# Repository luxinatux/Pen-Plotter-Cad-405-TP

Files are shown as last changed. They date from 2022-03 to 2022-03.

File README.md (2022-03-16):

# Pen-Plotter-Cad-405-TP
 This Repository was created to show the ME 405 pen-plotter CAD repository. It contains the STL files for print as well. This repository contains manufacturing pictures as well as documents necessary to build the project.

## **Description of Project**
Our Hardware Design is broken up into three parts: the drop down table base, the track, and the sled. The drop down table base allows us to have a half degree of freedom by being in up(pen down) or in the down position (pen up). We used a 12V continuous pull solenoid, actuated with an N-channel Mosfet with a 5V Gate to Source start voltage. This in conjuction with a flyback diode, and two 4 inch springs, allowed for our drawing surface to be dropped and not be in contact with the pen. The sled was the mover of the pen. Two 3D printed side rails created a track for our pen holder. The pen holder moved along this track being guided by 6mm GT2 timing belt that was directly mounted to the holder. The belt was driven by a 48 tooth plastic gear that was geared to the provided ME 405 bin Pittperson Gearmotors. The side rails were epoxied to a 4"x13"x0.375" piece of particle board with a slot cut through the middle of it. The conjunction of the drop down table base and the sled were through the "elbow motor". The "elbow motor" was a 131:1 12V DC motor that was clamped down to a 3D printed motor mount. This motor mount was epoxied to the top of the drop down table ledge, and the nucleo is mounted next to it. The elbow motor shaft ran through the particle board sled, and interfaced with a shaft collar epoxied to the surface. In order to allow free motion of the sled across the drawing plane, a caster wheel was epoxied to the end of the sled, opposite of the elbow motor and shaft collar. A sawed off skateboard truck provided an appropriate solution. The track for the skateboard wheel was created such that the sled would be level when moving left and right. To protect the system, two limit switches were added: one on the pen holder slider, and one on the skateboard wheel track. These two limit switches were used as zeroing points in our code.

The Bill of Materials is at the bottom of the README

## **Functional Prototype**
Included Below is a link to our plotter drawing a smiley face: 
https://youtu.be/C0HX3mLi9cc

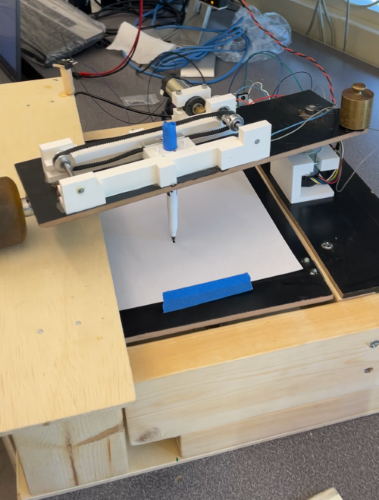
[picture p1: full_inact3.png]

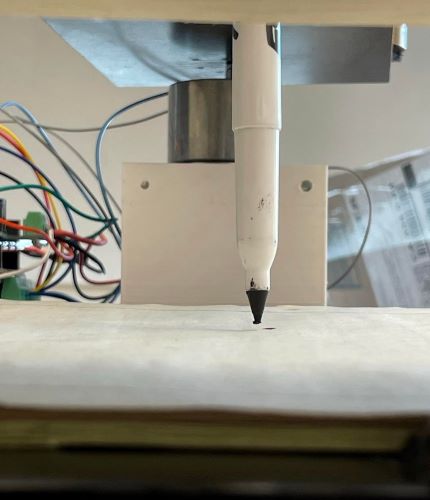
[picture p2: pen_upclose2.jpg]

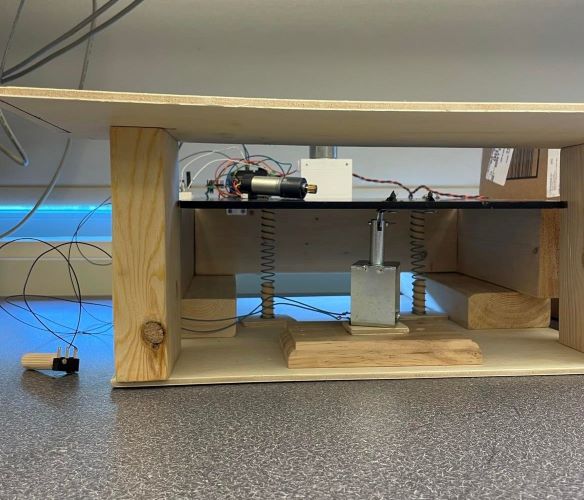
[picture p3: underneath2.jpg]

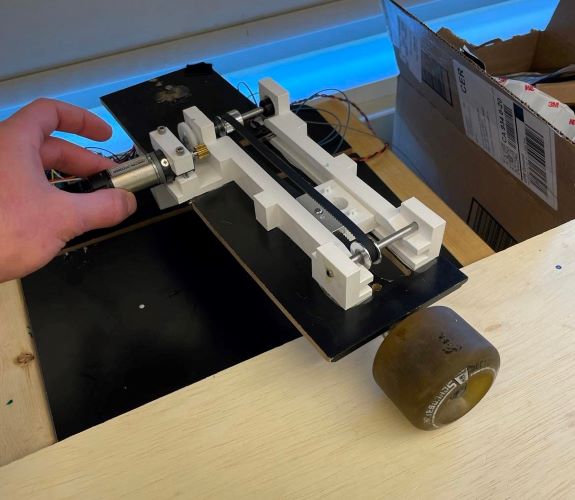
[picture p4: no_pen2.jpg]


## **CAD Model**
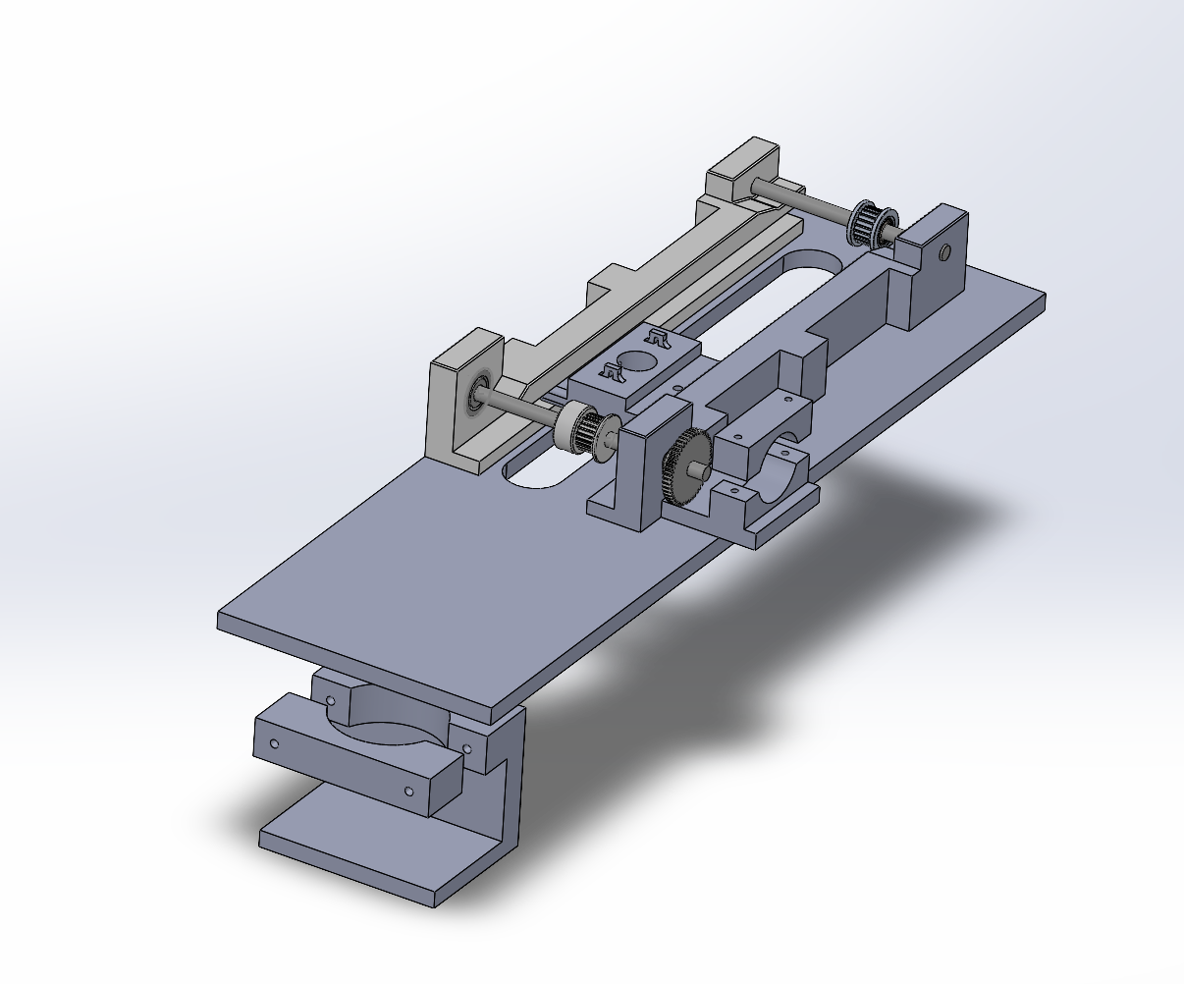
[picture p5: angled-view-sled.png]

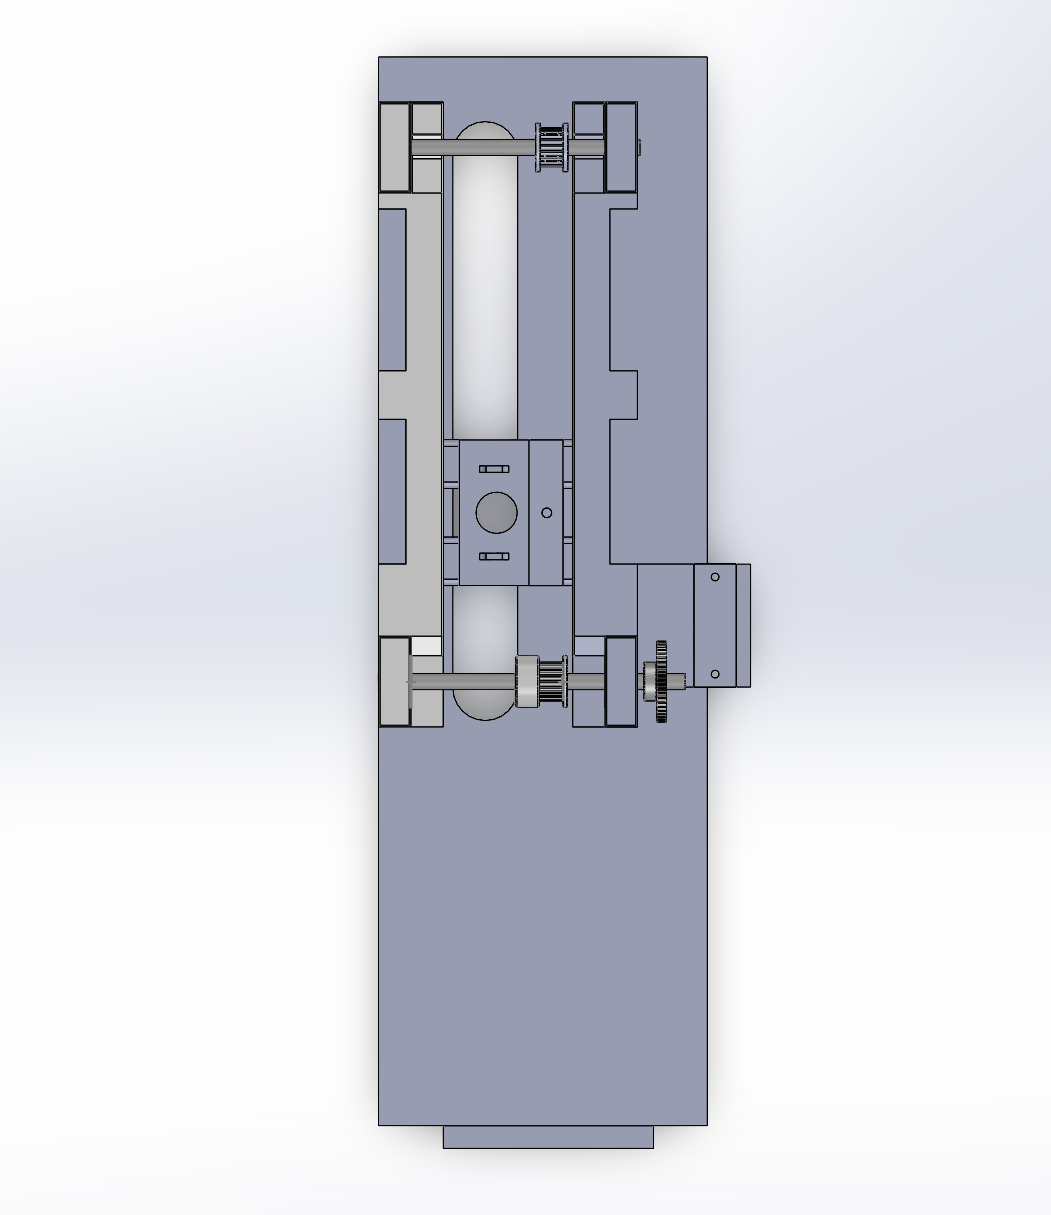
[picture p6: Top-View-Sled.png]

## **Drawings**
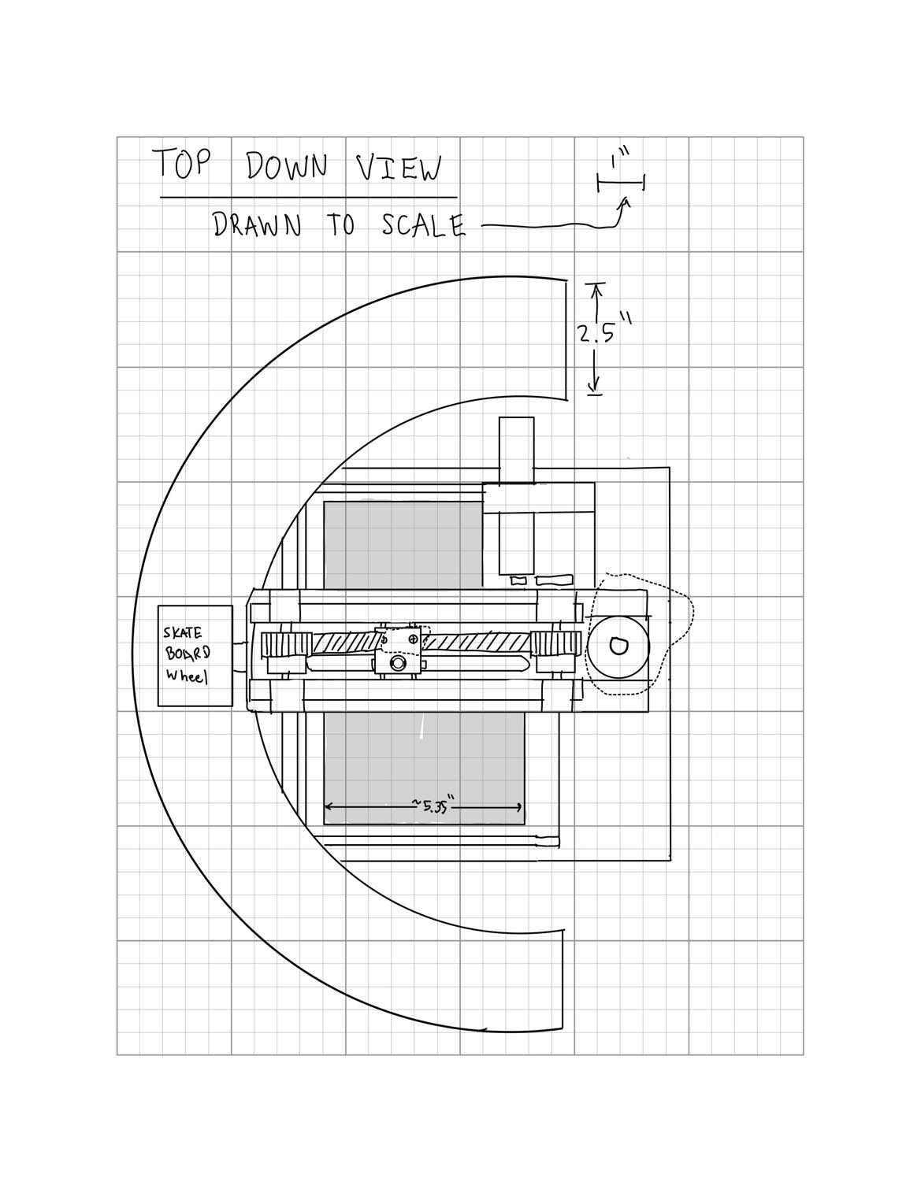
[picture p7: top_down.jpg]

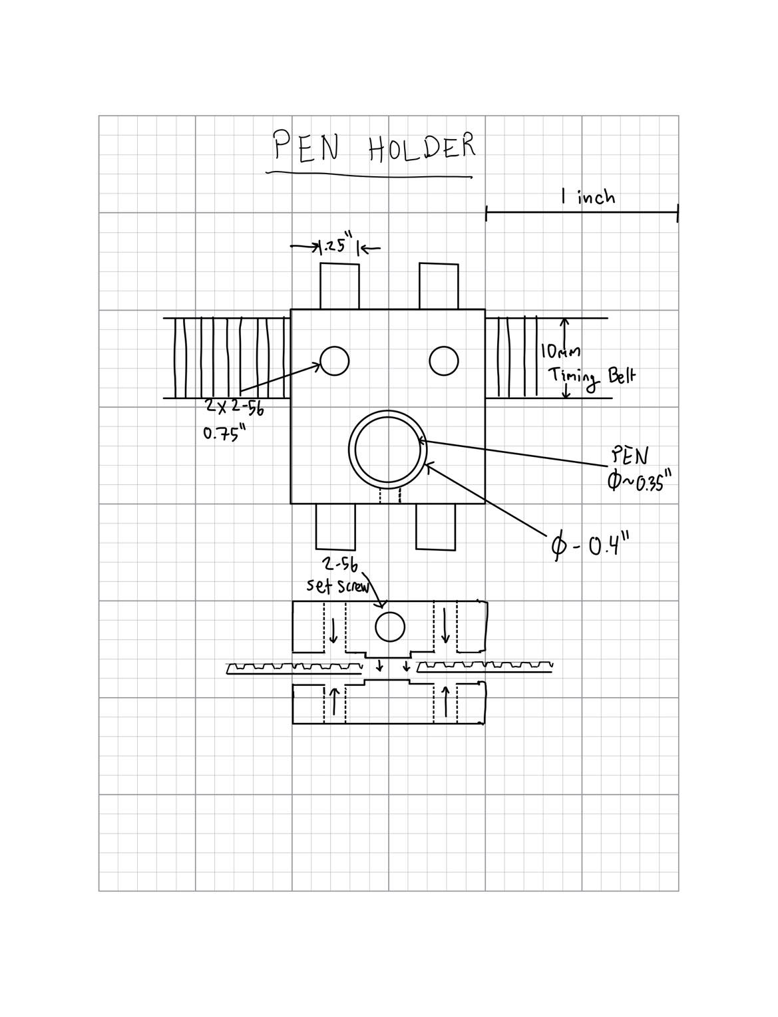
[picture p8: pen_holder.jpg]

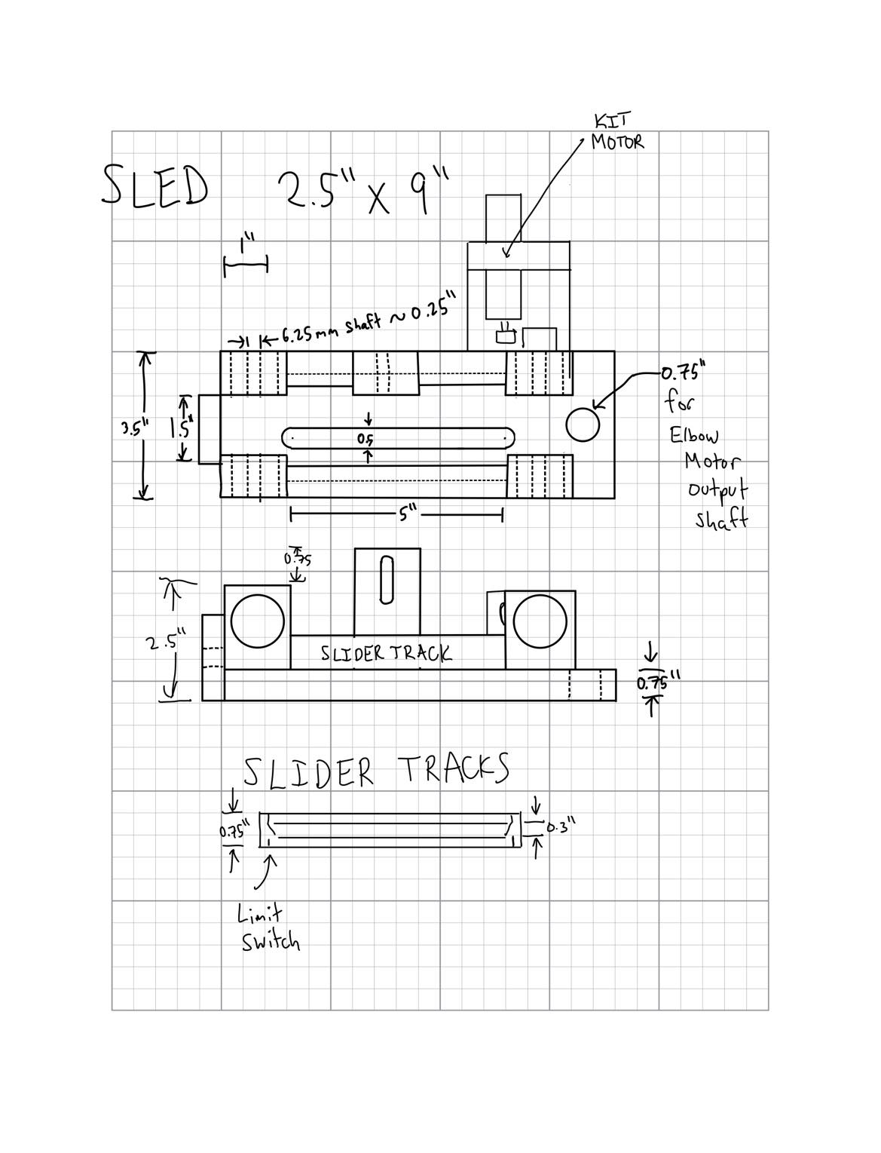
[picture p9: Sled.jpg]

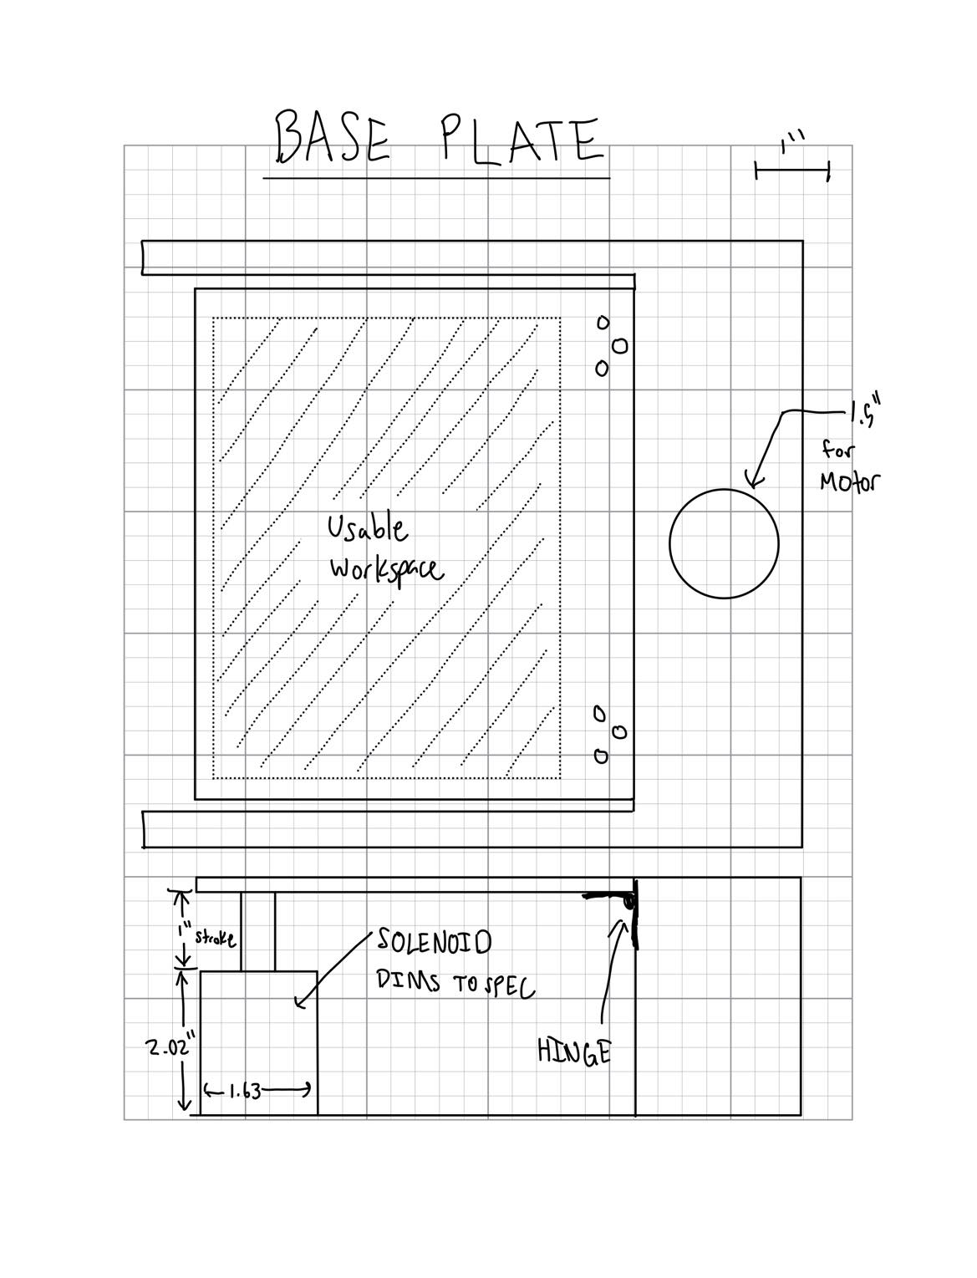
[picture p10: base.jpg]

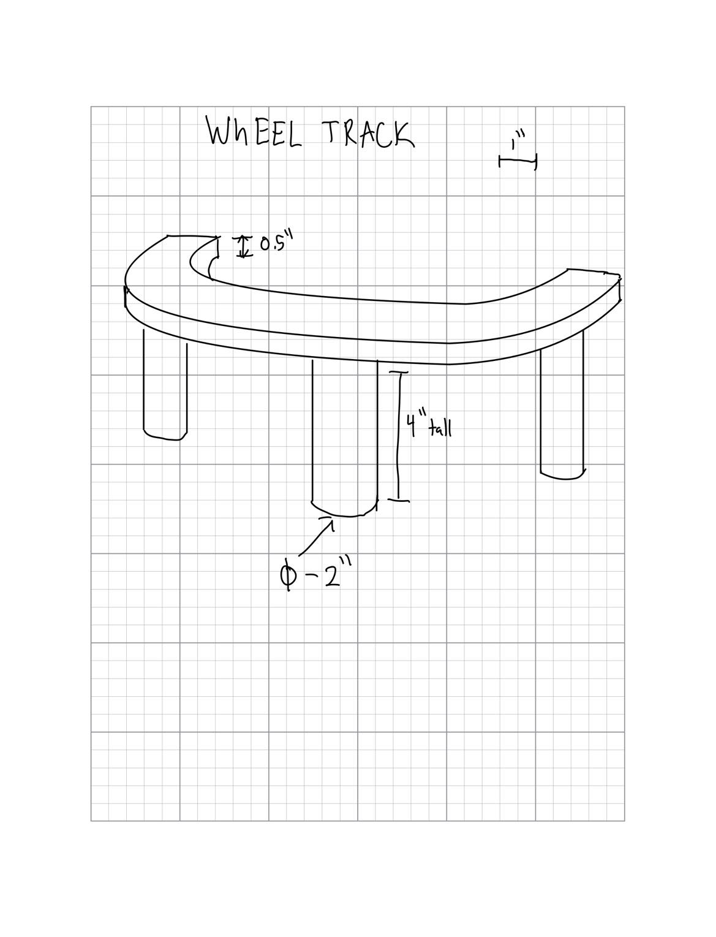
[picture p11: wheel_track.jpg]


## **Bill of Materials**
| Qty. | Part | Source | Cost |
|:----:|:---|:---|:---:|
|  1 | Pittperson Gearmotors | ME405 Tub | - |
|  1 | Nucleo with Shoe | ME405 Tub | - |
|  1 | Resistors, 100, 5.1K  | ME405Resistor Notebook| - |
|  1 | 131:1 12V DC Motor | DFrobot.com | $29.00  |
|  1 | Various Expo Markers  | Lucas Whiteboard | - |
|  1 | GT2 Timing Belt,Gear, | | |
| | Timing Pulley | Amazon.com | $17.39  |
|  1 | 12V Cont.Pull Solenoid| Digikey.com | $23.08  |
|  6 | Limit Switches | Digikey.com | $8.94 |
|  3 | MosfetN-ch,IRFP250NPBF| Digikey.com | $7.86 |
|  6 | Diode, 1N4007G-T | Digikey.com | $2.48 |
|  1 | Skateboard Wheels | Lucas Skateboard | - |
|  1 | 5mm Steel Shaft, 12in | McMaster Carr | $2.50 |
|  4 | 5mm Plastic Bearings  | McMaster Carr | $14.96  |
|  4 | 2ft 2x4 | Home Depot | - |
|  2 | 5 min Epoxy | Ace Hardware | - |
|  6 | 5mm shaft collars | McMaster Carr | $13.54  |
|  2 | 48T gear,2662N31 | McMaster Carr | $7.32 |
|  2 | 4" 0.5"D springs | Ace Hardware | $8.45 |

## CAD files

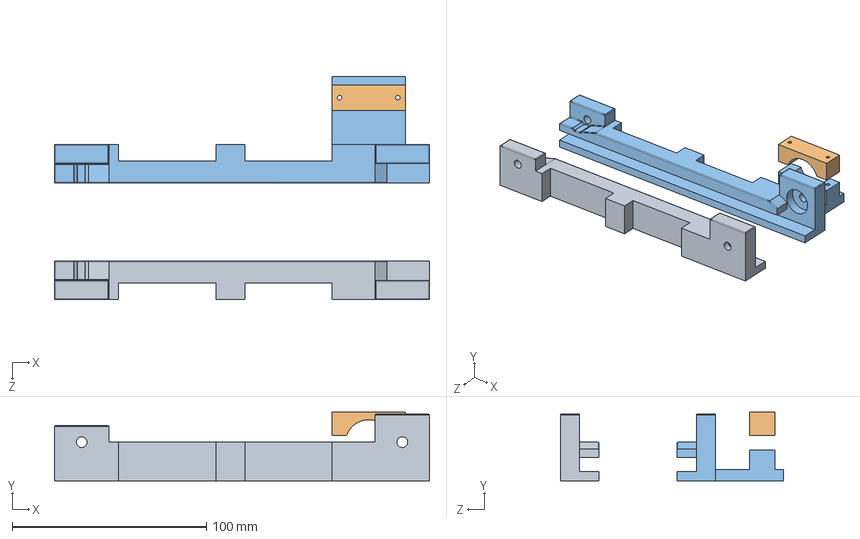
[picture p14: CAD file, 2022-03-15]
Solidworks 2021-2022/slider assem.SLDASM
193.0 x 35.5 x 115.0 mm
side_rail_left
wilton-block-motor
side_rail_right

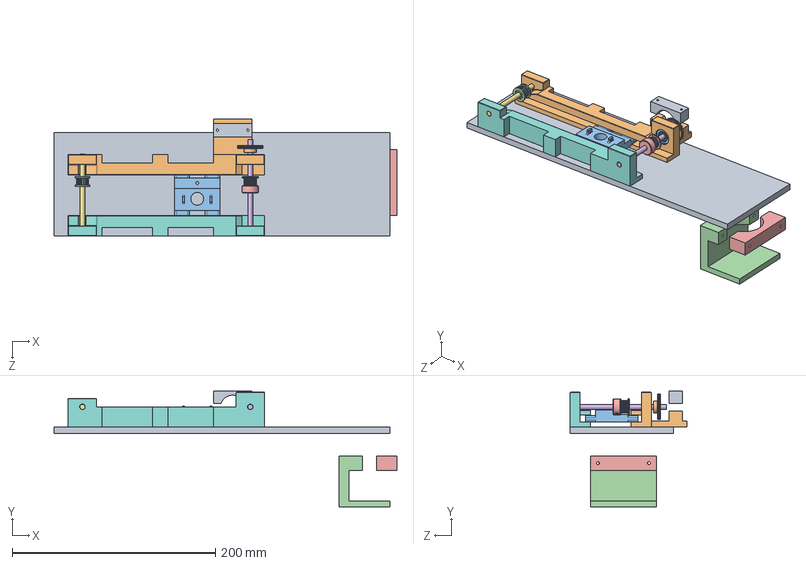
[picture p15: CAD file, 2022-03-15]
Solidworks 2021-2022/assembly_SLed.SLDASM
337.2 x 113.8 x 115.1 mm
base plate
2662N31_20 Degree Pressure Angle Plastic Gear
6455K92_Plastic Ball Bearing x 2
Gates_2GT_20T_Toothed_Idler
GT2_Pulley20_Teeth
driver_shaft
idler shaft
side_rail_left
wilton-block-motor
side_rail_right
holder
elbow_holder
wilton-block-elbow

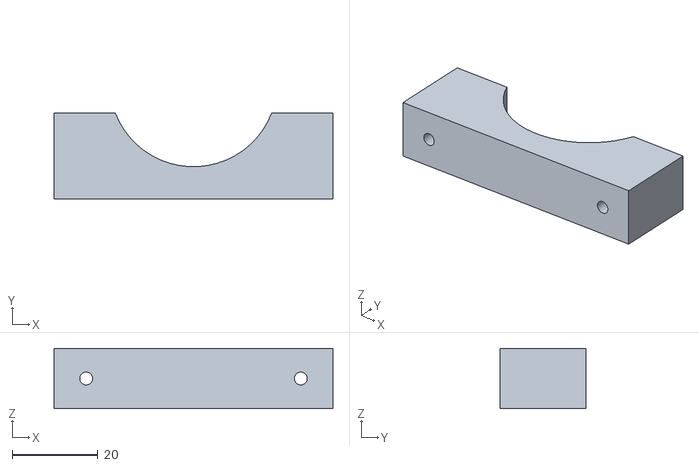
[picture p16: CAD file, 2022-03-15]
3D-print_STL/wilton-block-elbow.STL
65.0 x 20.0 x 14.0

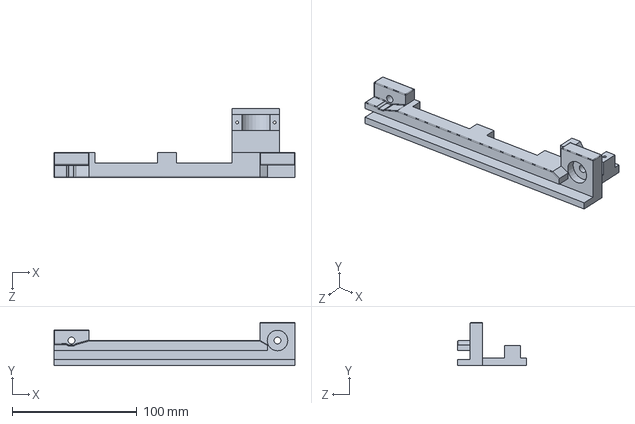
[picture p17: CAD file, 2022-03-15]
Solidworks 2021-2022/side_rail_right.SLDPRT
193.0 x 34.4 x 55.0 mm

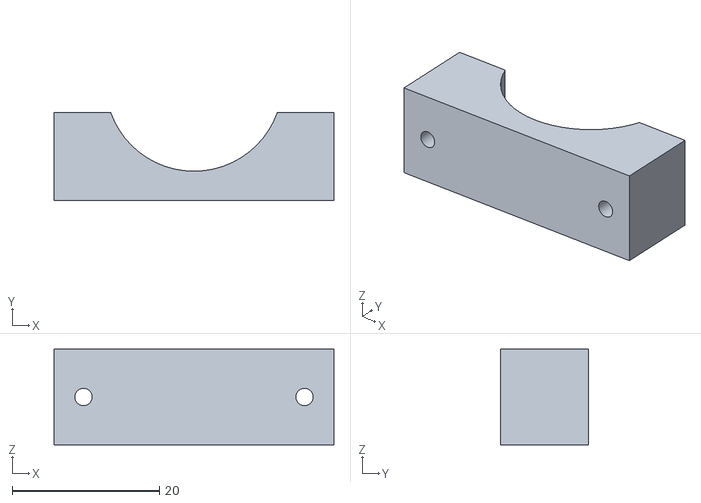
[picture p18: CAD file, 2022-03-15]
3D-print_STL/wilton-block-motor.STL
38.0 x 12.0 x 13.0

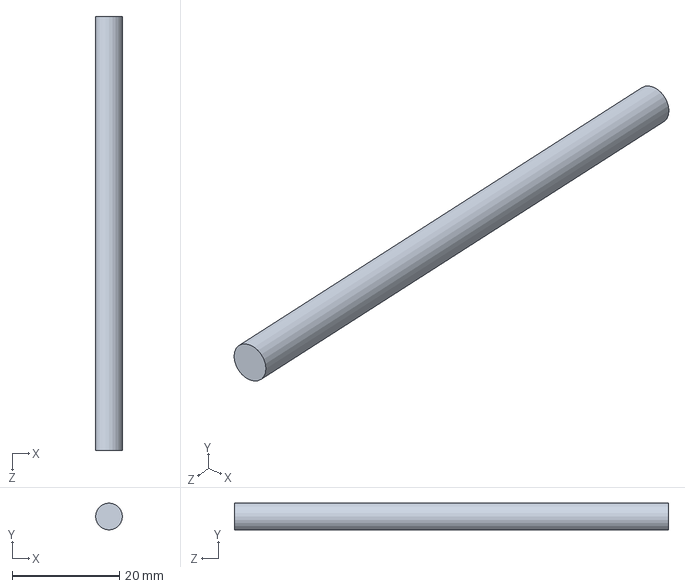
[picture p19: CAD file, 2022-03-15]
Solidworks 2021-2022/idler shaft.SLDPRT
5.00 x 5.00 x 80.8 mm

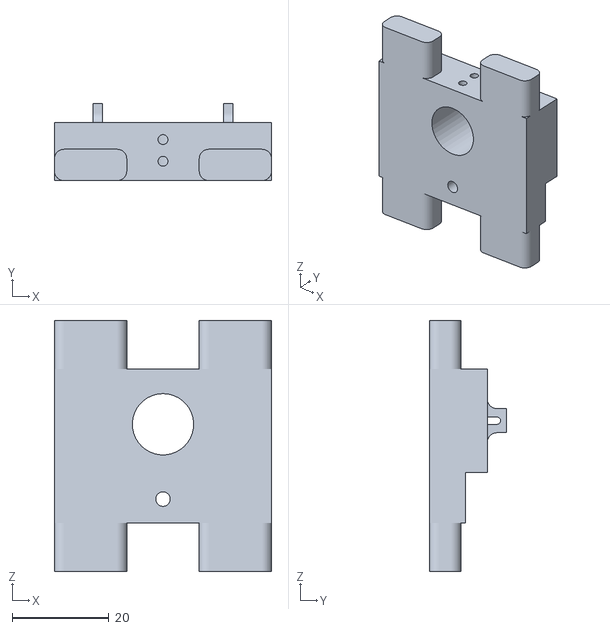
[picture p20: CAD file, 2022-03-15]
3D-print_STL/pen_holder.STL
45.0 x 16.0 x 52.0

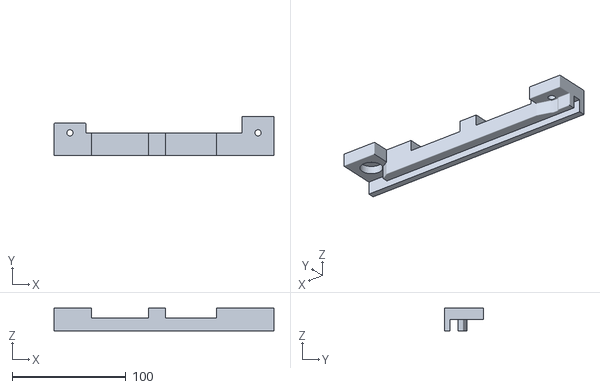
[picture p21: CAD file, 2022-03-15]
3D-print_STL/side_rail_left_3.0.STL
193.0 x 34.4 x 20.0

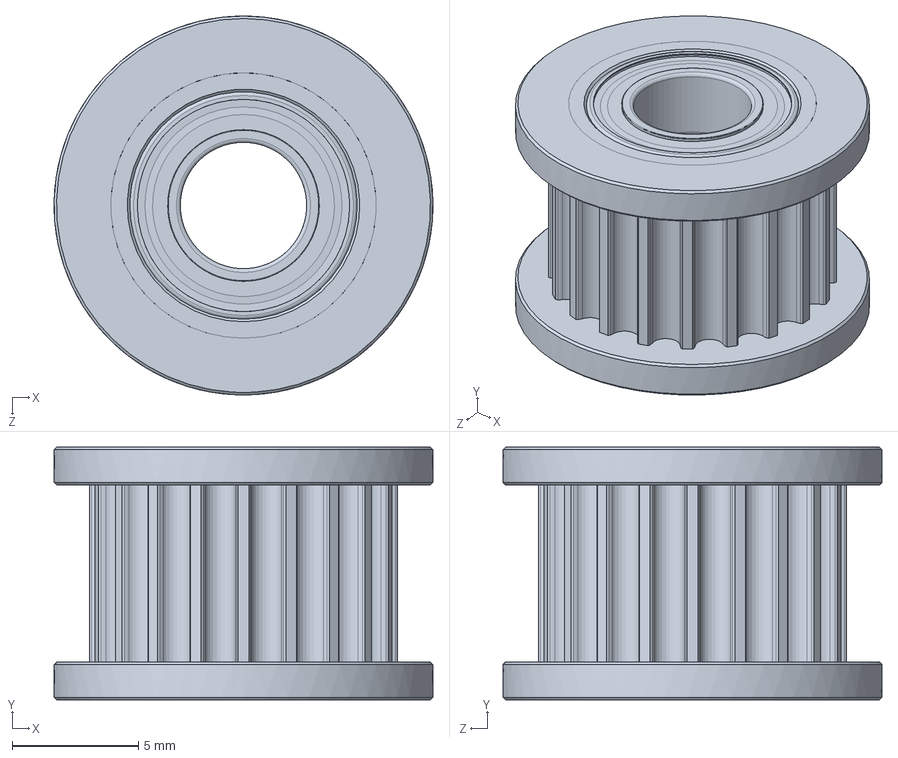
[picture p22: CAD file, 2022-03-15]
Solidworks 2021-2022/Gates_2GT_20T_Toothed_Idler.SLDPRT
15.0 x 10.0 x 15.0 mm

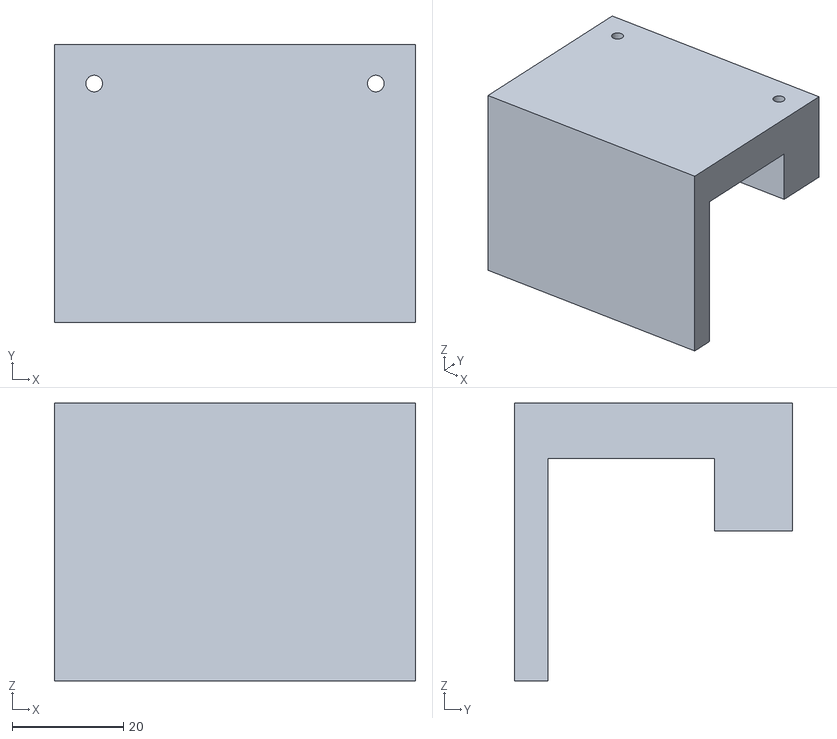
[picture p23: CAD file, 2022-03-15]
3D-print_STL/elbow_holder2.0.STL
65.0 x 50.0 x 50.0

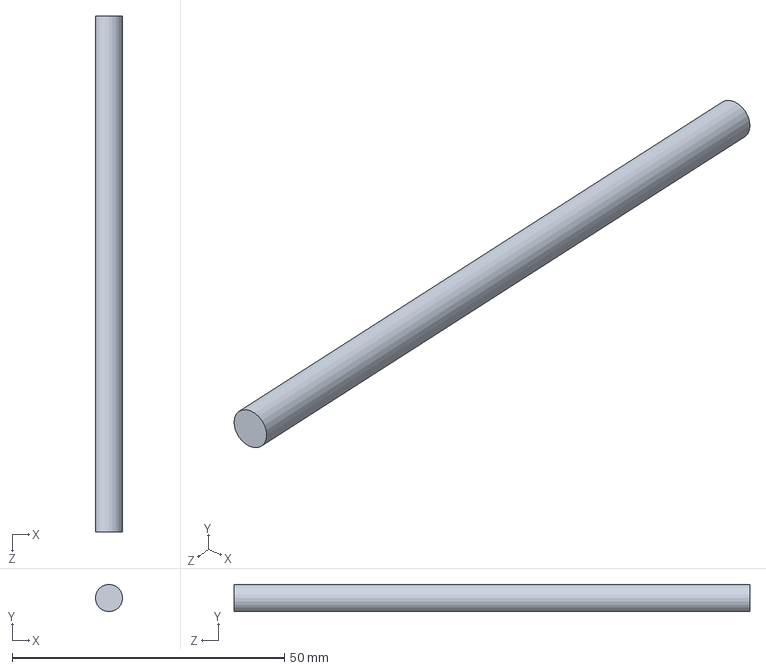
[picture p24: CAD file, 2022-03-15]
Solidworks 2021-2022/driver_shaft.SLDPRT
5.00 x 5.00 x 94.8 mm

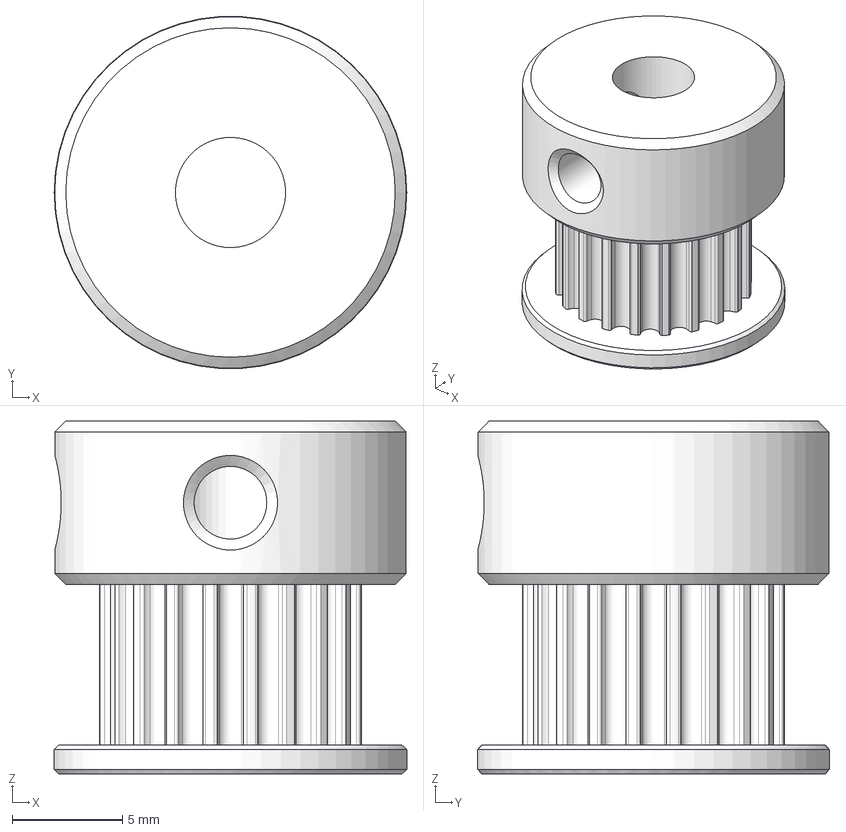
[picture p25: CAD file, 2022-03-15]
Solidworks 2021-2022/GT2_Pulley20_Teeth.stp
16.0 x 16.0 x 16.0 mm

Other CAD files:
3D-print_STL/side_rail_right_3.0.STL
Solidworks 2021-2022/wilton-block-elbow.SLDPRT
Solidworks 2021-2022/holder.SLDPRT
Solidworks 2021-2022/side_rail_left.SLDPRT
Solidworks 2021-2022/elbow_holder.SLDPRT
Solidworks 2021-2022/wilton-block-motor.SLDPRT
Solidworks 2021-2022/2662N31_20 Degree Pressure Angle Plastic Gear.SLDPRT
Solidworks 2021-2022/6455K92_Plastic Ball Bearing.SLDPRT
Solidworks 2021-2022/GT2_Pulley20_Teeth.SLDPRT
Solidworks 2021-2022/base plate.SLDPRT
